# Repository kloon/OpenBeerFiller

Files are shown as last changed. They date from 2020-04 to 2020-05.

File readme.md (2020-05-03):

# Open Beer Filler


Open Beer Filler is an Arduino Uno sketch for controlling a beer filling line. The idea was started by Christopher Harrison-Hawkes AKA [HarryBrew69 on YouTube](https://www.youtube.com/channel/UCIIYTzYpd8D7y816diZB0Dw). The sketch works by controlling a beer bottling line via a Arduino Uno and various sensors.

## Configuration
Before uploading the sketch to your Arduino Uno be sure to modify the InputConfig.h and Config.h files to map it to your microcontroller pins. We have mapped the pins to default so if you follow the Schematic below it should work out of the box.

### InputConfig.h Definitions
VARIABLE | DEFINITION
--- | ---
START_BUTTON | The pin on which the start button is attached
BEER_INLET_SOL_1 | The pin controlling the solenoid for beer tube 1
BEER_INLET_SOL_2 | The pin controlling the solenoid for beer tube 2
BEER_INLET_SOL_3 | The pin controlling the solenoid for beer tube 3
BEER_FILL_SENSOR_1 | The pin that senses when the fill sensor for beer tube 1 is triggered
BEER_FILL_SENSOR_2 | The pin that senses when the fill sensor for beer tube 2 is triggered
BEER_FILL_SENSOR_3 | The pin that senses when the fill sensor for beer tube 3 is triggered
CO2_PURGE_SOL | The pin controlling the solenoid for releasing CO2
FILL_RAIL_SOL | The pin controlling the solenoid for lifting and dropping the filler rail
BEER_BELT_SOL | The pin controlling the solenoid for moving the beer line forward

### Config.h Definitions
VARIABLE | DEFINITION
--- | ---
CO2_PURGE_PERIOD | How long in milliseconds to purge with CO2 before filling with beer
CO2_PURGE_RETRACTION_PERIOD | How long in milliseconds to purge with CO2 after filling with beer, this happes mid lifting the filler tubes.
CO2_PURGE_RETRACTION_DELAY | How long in milliseconds to wait before starting CO2 purge after starting to retract filler tubes.
FILLER_TUBE_MOVEMENT_DELAY | How long in milliseconds to wait after raising/lowering filler tube before starting the next action like opening the filling lines.
MOVE_BEER_BELT_PERIOD | How long in milliseconds to run the beer belt solenoid for, ie how long should the beer belt move.
FILL_SENSORS_TIMER_DELAY | How often in the background should the timer check the Fill sensors' status, defaults to every 100ms.
CONINUOUS_FILLING | If this definition is enabled it will put the sketch in continous filling mode, meaning once it is done filling it will auto start with the next batch. This is for production use.
FILL_SENSORS_TRIGGER | Sensitivity of the fill sensors, a value between 0 and 1023 representing the detected voltage.

### Required Libraries
- [TimerOne](https://playground.arduino.cc/Code/Timer1/)

## Schematic
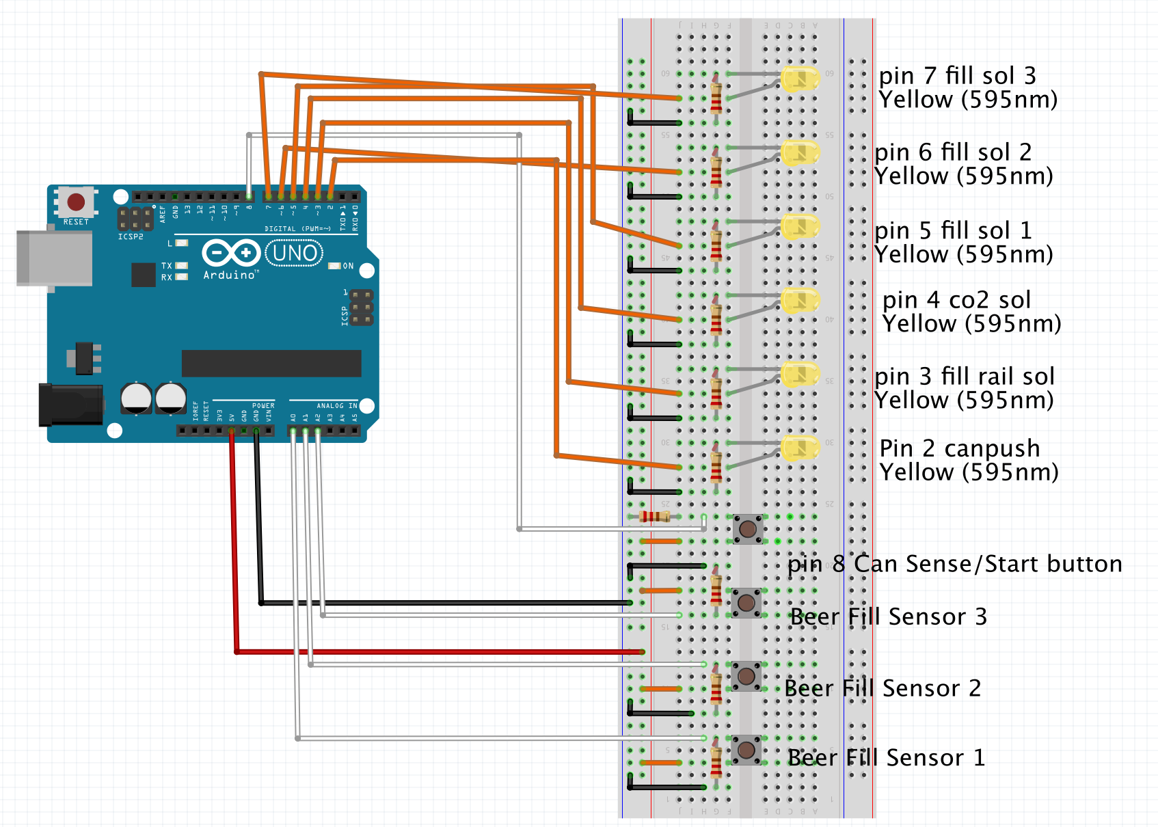
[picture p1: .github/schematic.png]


## Feature Requests
At present the sketch only supports the Arduino Uno, however we have plans in the works to introduce ESP8266 support with various other nice to have functionality such as remote setup, monitoring and control via a built in web page.

## Open Source
The project is completely Open Source licensed under the GPL version 3 or above so you are free to use this code as long as you just give attribution. If you have the ability to help us out then please feel free to submit pull requests or even just log issues for bugs or feature request.

## Troubleshooting

### Missing InputConfig.h & Config.h files in your build
If you are getting errors when trying to compile this sketch about missing Config.h and/or InputConfig.h files then it means your Arduino IDE is not picking up these files as part of the sketch. This is likely just an includes folder config error so check your includes folder paths.

It is also possible you are running an outdated version of the Arduino IDE, in that case ensure you are running version 1.8.10+ of the Arduino IDE.

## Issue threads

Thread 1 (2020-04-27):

All stop feature

pleonber, 2020-04-27:
I recommend implementing a "all stop" feature.   This would be a button (you can use the start button for this) to stop machine at any point.

Based on earlier concepts I designed a state machine which will allow the can filler to stop from any state.   I'll attached the code here for reference purposes.

[can_filler_state_maching_example.txt](https://github.com/kloon/OpenBeerFiller/files/4537195/can_filler_state_maching_example.txt)

BaggyLala, 2020-04-28:
Thanks for the input "All stop" feature is now considered within the code. An additional button will be added to the build that is attached to the controllers reset pin. This way any power interruptions will also set the machine back to a known state with all the valves shut etc.
In the event of any major reworking of this code being required we will certainly look again at the approach used in your example text file.

Closed 2020-04-28.

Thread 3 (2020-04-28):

Use interrupts for beer sensing

kloon, 2020-04-28:
The current code utilises a while loop for sensing when a bottle/can has reached its full capacity, the problem with this is that it causes  a block in the main program loop which is not ideal.

Using interrupts we can eliminate this while loop block in the main loop allowing for other critical functionality that relies on the main loop to execute flawlessly.

The problem we need to solve is that there's only two interrupt pins on the Uno and we require a lot more to monitor the three filling solenoids as well as a kill switch.

The solution would be to look at ways we can utilise a single pin and attach multiple interrupts and inputs on that pin.

This issue is only present with the Arduino Uno, the ESP8266 supports interrupts on all its digital pins.

Closed 2020-05-01.

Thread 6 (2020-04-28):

Backfill as filler tubes are raised

kloon, 2020-04-28:
When the filler tubes are raised the volume they displaced while being inserted will need to be topped up.

An idea would be to reopen the filler tubes after x amount of retraction for a short period.

KINGGarry, 2020-07-19:
I agree.  Our tubes occupies 14ml in each can.

lalo-uy, 2020-07-19:
And a little co2 after that will provide foam over the beer, to avoid air below the cap.

interstaller555, 2020-10-10:
I run a “real” 3 head canner - microcanner flex - and the burp of CO2 pre-lid placement takes care of that - that’s pretty much industry standard.

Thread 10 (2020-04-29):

Use millis instead of delay

kloon, 2020-04-29:
Currently, there are still some blocking function calls running that relies on using `delay()` for waiting before another function/event fires.

Using `mills()` combined with more program states instead of `delay()` we can eliminate all these blocking calls ensuring the main loops stays non-blocking.

See [this tutorial](https://www.norwegiancreations.com/2017/09/arduino-tutorial-using-millis-instead-of-delay/) for more details on `millis()` benefit over `delay()` and how to use it.

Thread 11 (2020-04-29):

Idea for adding analog code to read beer in a tin or bottle

Adamzsite, 2020-04-29:
Is this code right,

void triggerFullFillSensor1() {
  Serial.println( "Beer fill sensor 1 triggered" );
  // Close beer inlet solenoid.
  digitalWrite(BEER_INLET_SOL_1, LOW)&&((BEER_FILL_SENSOR_1)<400));
  fillSensor1Triggered = true;
}

Closed 2020-05-03.

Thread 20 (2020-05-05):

Run start - calibration routine needed

BaggyLala, 2020-05-05:
fill cans lower probe, take reading store locally for this run then push up to web service. all done through the LCD and buttons

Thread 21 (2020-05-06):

Add LCD/LED display support

kloon, 2020-05-06:
Add support for LCD/LED displays with menu functionality. This will be used for basic configuration and information display.

franknh-design, 2020-10-08:
Information like counting when the button is pressed ex. first button press 3 bottle, second press 6 bottle and so on. Then you dont have to count by your self 💯

interstaller555, 2020-10-12:
what about using an inductive sensor for counting cans and measuring when there are 3 total so you're not potentially missing one can on a fill....

lalo-uy, 2020-10-12:
Cans are aluminum, wont register on inductive sensor. Will need an optical
one.

El El lun, 12 de oct. de 2020 a la(s) 10:24, interstaller555 <
notifications@github.com> escribió:

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

interstaller555, 2020-10-12:
I hate to say it man - but that's not the case.
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

This is on my machine at work... and these are the sensors.

https://www.automationdirect.com/adc/shopping/catalog/sensors_-z-_encoders/inductive_proximity_sensors/12mm_round_harsh_duty/stainless_steel_factor_1_sensing_(12mm)/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

interstaller555, 2020-10-12:
I love this project so much and it has such potential! you guys are doing an amazing job!!! I run the brewery I work at and we have a canning line so I'd be more then happy to help with design or technical questions. I'm also working on my own integration of this so I can document and provide support for my iteration. I sent Kloop and email - if you DM me I can send you a copy.

kloon, 2020-10-13:
> Cans are aluminum, wont register on inductive sensor. Will need an optical one.

One would think it won't but it actually does. 3D Printers use the same inductive sensors with aluminum heat beds and it works 100%.

Opened a new issue to take a look #26 and for further discussion.

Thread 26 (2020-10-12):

Add support for an inductive can counting sensor

kloon, 2020-10-12:
Introduce an inductive sensor placed beneath the first can filling tube that can count cans as they pass the sensor. Having a sensor in place we can prevent opening the filling tubes when there are no cans underneath them.

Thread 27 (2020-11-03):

Issue with Fill Sensors

jnr-nat, 2020-11-03:
I have the code all running and all works well when I touch the fill sensor to the filler tube. The issue is it does not trigger when in liquid. I have confirmed the voltage when submerged in beer (filler tube in liquid, multimeter on sensor wire, and in beer). It shows 5v, but does not trigger the solenoid to close. Any suggestions?

I'm running a 2.2K resistor between Analog ports and Neg

Closed 2020-11-03.

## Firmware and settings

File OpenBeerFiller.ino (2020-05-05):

/**
 * Open Beer Filler
 * Copyright (c) 2020 Gerhard Potgieter [https://gerhardpotgieter.com]
 *
 * Based on an idea by Christopher Harrison-Hawkes [https://harrisonsbrewery.com]
 *
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
 */
#pragma once;

// Library includes.
// AVR(UNO) Libraries.
#ifdef __AVR__
#include <TimerOne.h>;
#endif;

// Project specific includes.
#include "Config.h";
#include "InputConfig.h";

/**
 * ***************************************************************************
 * ******************************* VARIABLES *********************************
 * ***************************************************************************
 */
volatile bool fillSensor1Triggered = false;
volatile bool fillSensor2Triggered = false;
volatile bool fillSensor3Triggered = false;
bool idleMessageDisplayed = false;
enum ProgramState {UNDEF,IDLE,START,FILLING,STOP};
ProgramState currentState = UNDEF;

/**
 * ***************************************************************************
 * ******************************** FUNCTIONS ********************************
 * ***************************************************************************
 */
void setupPins() {
  // Filler solenoids.
  pinMode(BEER_INLET_SOL_1, OUTPUT);
  pinMode(BEER_INLET_SOL_2, OUTPUT);
  pinMode(BEER_INLET_SOL_3, OUTPUT);

  // CO2 solenoid.
  pinMode(CO2_PURGE_SOL, OUTPUT);

  // Fill rail solenoid.
  pinMode(FILL_RAIL_SOL, OUTPUT);

  // Beer belt solenoid.
  pinMode(BEER_BELT_SOL, OUTPUT);

  // Fill sensors.
  pinMode(BEER_FILL_SENSOR_1, INPUT);
  pinMode(BEER_FILL_SENSOR_2, INPUT);
  pinMode(BEER_FILL_SENSOR_3, INPUT);

  // Start/Stop button.
  pinMode(START_BUTTON, INPUT);
}

/**
 * Setup a non-blocking interrupt timer for checking the fill sensors.
 */
void setupFillSensorsTimer() {
  Timer1.initialize(FILL_SENSORS_TIMER_FREQUENCY);
  Timer1.attachInterrupt(checkFillSensors);
}

/**
 * Check if the fill sensors have been triggered.
 */
void checkFillSensors() {
  if (FILL_SENSORS_TRIGGER < analogRead(BEER_FILL_SENSOR_1)) {
    triggerFullFillSensor1();
  }
  if (FILL_SENSORS_TRIGGER < analogRead(BEER_FILL_SENSOR_2)) {
    triggerFullFillSensor2();
  }
  if (FILL_SENSORS_TRIGGER < analogRead(BEER_FILL_SENSOR_3)) {
    triggerFullFillSensor3();
  }
}

/**
 * Fired when fill sensor 1 is triggered as full.
 */
void triggerFullFillSensor1() {
  if (!fillSensor1Triggered && hasProgramState(FILLING)) {
    closeBeerFillerTube(BEER_INLET_SOL_1);
    fillSensor1Triggered = true;
    Serial.println("Filler tube 1 closed");
  }
}

/**
 * Fired when fill sensor 1 is triggered as full.
 */
void triggerFullFillSensor2() {
  if (!fillSensor2Triggered && hasProgramState(FILLING)) {
    closeBeerFillerTube(BEER_INLET_SOL_2);
    fillSensor2Triggered = true;
    Serial.println("Filler tube 2 closed");
  }
}

/**
 * Fired when fill sensor 1 is triggered as full.
 */
void triggerFullFillSensor3() {
  if (!fillSensor3Triggered && hasProgramState(FILLING)) {
    closeBeerFillerTube(BEER_INLET_SOL_3);
    fillSensor3Triggered = true;
    Serial.println("Filler tube 3 closed");
  }
}

/**
 * Return whether all fill sensors have been triggered or not.
 */
bool allFillSensorsTriggered() {
  return fillSensor1Triggered && fillSensor2Triggered && fillSensor3Triggered;
}

void resetFillSensorTriggers() {
  fillSensor1Triggered = fillSensor2Triggered = fillSensor3Triggered = false;
}

/**
 * Open a single beer filler solenoid.
 */
void openBeerFillerTube(int fillerTubePin) {
  digitalWrite(fillerTubePin, HIGH);
}

/**
 * Close a single beer filler solenoid.
 */
void closeBeerFillerTube(int fillerTubePin) {
  digitalWrite(fillerTubePin, LOW);
}

/**
 * Open all beer filler solenoids.
 */
void openAllBeerFillerTubes() {
  Serial.println("Opening all beer filler tubes");
  digitalWrite(BEER_INLET_SOL_1, HIGH);
  digitalWrite(BEER_INLET_SOL_2, HIGH);
  digitalWrite(BEER_INLET_SOL_3, HIGH);
}

/**
 * Close all beer filler solenoids.
 */
void closeAllBeerFillerTubes() {
  Serial.println("Closing all beer filler tubes");
  digitalWrite(BEER_INLET_SOL_1, LOW);
  digitalWrite(BEER_INLET_SOL_2, LOW);
  digitalWrite(BEER_INLET_SOL_3, LOW);
}

/**
 * Open the CO2 purge solenoid, wait a while and then close it again.
 */
void purgeCO2( bool retract = false ) {
  Serial.println("Purging CO2");
  digitalWrite(CO2_PURGE_SOL, HIGH);
  if(!retract) {
    delay(CO2_PURGE_PERIOD);
  } else {
    delay(CO2_PURGE_RETRACTION_PERIOD);
  }
  digitalWrite(CO2_PURGE_SOL, LOW);
}

/**
 * Raise the fillter tubes out of the bottles.
 */
void raiseFillerTubes() {
  Serial.println("Raising filler tubes");
  digitalWrite(FILL_RAIL_SOL, HIGH);
  delay(CO2_PURGE_RETRACTION_DELAY); // We use CO2_PURGE_RETRACTION_DELAY here as we want to start purging with CO2 as the fill rail raises.
}

/**
 * Lower the filler tubes into the bottles.
 */
void lowerFillerTubes() {
  Serial.println("Lowering filler tubes");
  digitalWrite(FILL_RAIL_SOL, LOW);
  delay(FILLER_TUBE_MOVEMENT_DELAY);
}

/**
 * Move the beer belt, wait a while and then stop it again.
 */
void moveBeerBelt() {
  Serial.println( "Moving beer belt" );
  digitalWrite(BEER_BELT_SOL, HIGH);
  delay(MOVE_BEER_BELT_PERIOD);
  digitalWrite(BEER_BELT_SOL, LOW);
}

/**
 * Code to run when we are in the IDLE ProgramState
 */
void idleState() {
  if (!idleMessageDisplayed) {
    Serial.println("Press Start Button to proceed");
    idleMessageDisplayed = true;
  }
  readStartButton();
}

/**
 * Code to run when we are in the START ProgramState.
 */
void startState() {
  moveBeerBelt();
  lowerFillerTubes();
  purgeCO2();
  openAllBeerFillerTubes();
  changeProgramState(FILLING);
}

/**
 * Code to run when we are in the FILLING ProgramState.
 */
void fillingState() {
  // Check if we are done filling.
  if(allFillSensorsTriggered()){
    raiseFillerTubes();
    purgeCO2(true);
    resetFillSensorTriggers();
    // If done filling, check if we want to do continuous filling or go back to the UNDEF state.
    #if defined(CONINUOUS_FILLING)
      changeProgramState(START);
    #else
      changeProgramState(IDLE);
    #endif;
  }
}

/**
 * Code to run when we are in the STOP ProgramState.
 */
void stopState() {
  // Reset the sensors and change ProgramState to UNDEF.
  resetUnit();
  changeProgramState(IDLE);
}

/**
 * Read the start button.
 */
void readStartButton() {
  if(
    HIGH==digitalRead(START_BUTTON)
    && hasProgramState(IDLE)
  ) {
    Serial.println("Start Button Pressed");
    changeProgramState(START);
  }
}

/**
 * Read the stop button.
 */
void readStopButton() {
  if(
    HIGH==digitalRead(START_BUTTON)
    && !hasProgramState(IDLE)
    && !hasProgramState(START)
  ) {
    Serial.println("Stop Button Pressed");
    changeProgramState(STOP);
  }
}

/**
 * Reset the unit,
 */
void resetUnit() {
  Serial.println("Reseting unit");
  closeAllBeerFillerTubes();
  digitalWrite(BEER_BELT_SOL, LOW);
  raiseFillerTubes();
  digitalWrite(CO2_PURGE_SOL, LOW);
  Serial.println("Done resetting unit");
  changeProgramState(IDLE);
}

/**
 * Change the ProgramState
 */
void changeProgramState(ProgramState state) {
  // Reset the bool to avoid the IDLE state message to repeat continiously.
  if (IDLE == state){
    idleMessageDisplayed = false;
  }
  currentState = state;
  Serial.print("Program state changed: ");
  Serial.println(currentState);
}

/**
 * Check if the currentState matches the passed state.
 */
bool hasProgramState(ProgramState state) {
  if(state == currentState) {
    return true;
  }
  return false;
}

/**
 * Code in this function must always run, avoid delays in here.
 */
void alwaysRun() {
  readStopButton();
}

/**
 * ***************************************************************************
 * ***************************** MAIN FUNCTIONS ******************************
 * ***************************************************************************
 */

/**
 * Main setup routine.
 */
void setup() {
  Serial.begin(115200);//Serial.begin(9600);
  setupPins();
  setupFillSensorsTimer();
  resetUnit();
}

/**
 * The main program loop, where all the magic comes togetger.
 */
void loop() {
  switch(currentState) {
    case IDLE:
      idleState();
      break;
    case START:
      startState();
      break;
    case FILLING:
      fillingState();
      break;
    case STOP:
      stopState();
      break;
  }
  alwaysRun();
}

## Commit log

2020-04-20 Dont forget ICACHE_RAM_ATTR for interrupt functions
2020-04-20 No need to run pinMode on interrupt pins.
2020-04-24 Added a wait time for filling tube movement.
    Added a int valve for the filling tubes to move..
2020-04-24 Move the C02 purge before the Beer valves open.
    move line 185 up to 184
2020-04-25 Changed a few things
    Added a button to start the program, this will have to be press on ever run, Im not sure if this best code for the job we could use a attachInterrupt?
    also moved the moveBeerBelt(); to the start of the loop, this means the unit load its self on start up
2020-04-26 Add files via upload
    This is the test layout of the Uno and Bread Board.
2020-04-26 Remove interrupts for now, read sensors via loop
2020-04-26 Remember to turn off fill solenoids.
2020-04-26 Add some serial prints when closing filler tubes.
2020-04-26 Remove delay to avoid button presses not being picked up.
    [OpenBeerFiller.ino]
2020-04-26 Add functionality and options to control purging the bottle tops with CO2 as the filler tubes retract.
2020-04-26 Move image to .github, update readme with more details and schematic
2020-04-26 Update schematic based on latest fritzing file
2020-04-26 Rename fritzing schematic
    [schematic.fzz]
2020-04-26 Update schematic screenshot
2020-04-26 Add files via upload
    Sketch Up File of the stainless Steel Frame design
2020-04-27 Add a a master reset.
    If you have a problem a you can press a button and the unit restarts, then runs a code to close all values and reset rams.
    [OpenBeerFiller.ino]
2020-04-28 Move the fill sensor checking out of the loop into an interrupt timer, to avoid blocking the main loop.
    [Config.h, OpenBeerFiller.ino]
2020-04-28 Remove old interrupt code
2020-04-29 Add TimerOne library to compile test workflow
2020-04-29 Use volatile variables for the interrupt variables.
2020-04-29 Change definition name for the timer to reflect it better.
2020-04-29 Move the default switch check to the top and remove the break to ensure it runs on every loop while also continuing with the other switch statements.
2020-05-01 Refine how the timer interrupts detect a fill sensor trigger to be more reliable, adjust the start button code a bit.
2020-05-01 First go at analog reading the voltage for the fill sensors
2020-05-03 Only trigger the fill sensors while filling
2020-05-03 Remove debugging serial print
2020-05-05 Corrected pin mode on input sensors
    set as output need to be input
    [OpenBeerFiller.ino]

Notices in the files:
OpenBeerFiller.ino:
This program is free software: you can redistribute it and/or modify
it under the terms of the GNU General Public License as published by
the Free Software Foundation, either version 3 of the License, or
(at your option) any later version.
